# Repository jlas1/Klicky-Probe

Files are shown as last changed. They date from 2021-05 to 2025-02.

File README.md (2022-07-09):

# Klicky Probe
Microswitch probe with magnetic attachment, primarily aimed at CoreXY 3d printers.

Initially it was focused on the [Voron printers](https://vorondesign.com/) (V2.4, V1.8, Trident, V0) and derivatives, now it's been restructured to better allow other printers to be documented here.

The objectives for this project are:
- drop in replacement for Omron TL-Q5MC2 or PL-08N2 (you don't need to replace the toolhead), replacement of BLtouch probes
- soldering not required
- minimal adjustments required
- be able to detect all the print surfaces
- be as close to the hotend tip as possible
- highly repeatable and accurate probes
- less temperature variations
- no melting of its parts
- cheap to build
- reuse spare parts if possible

Most of the Klicky probe users are using klipper, there are some macros in here that ease the probing process, by automating the attach, dock and use of the probe.

Some work has been developed to have the same functionality on RRF.

It can also be used with the [automatic Z calibration](https://github.com/protoloft/klipper_z_calibration) klipper plugin to effectively calculate the Z offset from the probe and from the Z endstop if your printers supports a Z endstop triggered by the nozzle (like most Voron's do)

The inspiration for the Klicky Probe comes from the [Quickdraw](https://github.com/Annex-Engineering/Quickdraw_Probe) and the [Euclid probe](https://github.com/nionio6915/Euclid_Probe), it uses some concepts from each of the projects.

Updated instructions provided by StefanRaatz.
oc_geek and TurBoxxs were also a great help in refining and testing the CAD files.
Garrettwp provided the initial revised macro files.
User richardjm revised the macro variables and added some functions.
Mental created the initial macro and one of the first magnetically attached microswitch probes.

Without them, and some others this effort would not be in the current state, many thanks to them all.

It is working very well, if you decide to use it, give me feedback, either here, or on discord, my discord user is JosAr#0517.

If you want to donate something regarding this project, use this [link](https://paypal.me/Josar154) or [__Buy me some ABS!__](https://www.buymeacoffee.com/JosAr), thanks

# Upgrading from an earlier version

If you are upgrading from an earlier version, check the [klipper macros](./Klipper_macros) folder, it contains update instructions.

# Probe options

Right now, there are two probe attachment options, each with two probe types.

## Regular Klicky

First klicky probe, based on the [Quickdraw probe](https://github.com/Annex-Engineering/Quickdraw_Probe), with an added third magnet for added stability and fixed dock gantry setups.

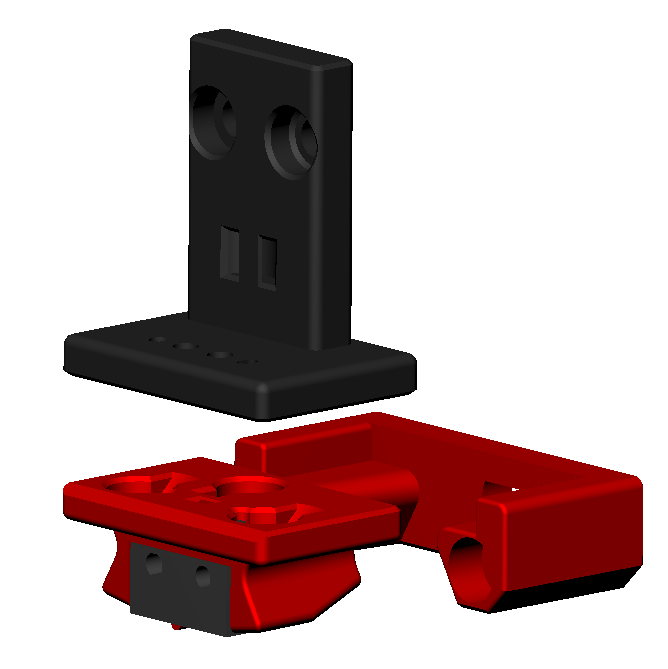
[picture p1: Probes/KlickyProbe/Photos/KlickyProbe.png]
klickyprobe


It uses magnets to secure the probe to the mount and also to make the electrical connection.
The magnets can be glued to prevent them from coming loose.
It supports a [microswitch probe](./Probes/KlickyProbe/) and [Unklicky](./Probes/Unklicky/) ([invented by DustinSpeed](https://github.com/majarspeed/Unklicky)) (self built probe, that so far surpasses the microswitches in common use) based probing.

### [Assembly instruction](./Probes/KlickyProbe/)

## KlickyNG

New enclosed magnets probe, it does not require glue to help prevent the magnets from coming loose, magnets are also self aligning.
This approach only uses common and easy to source parts.

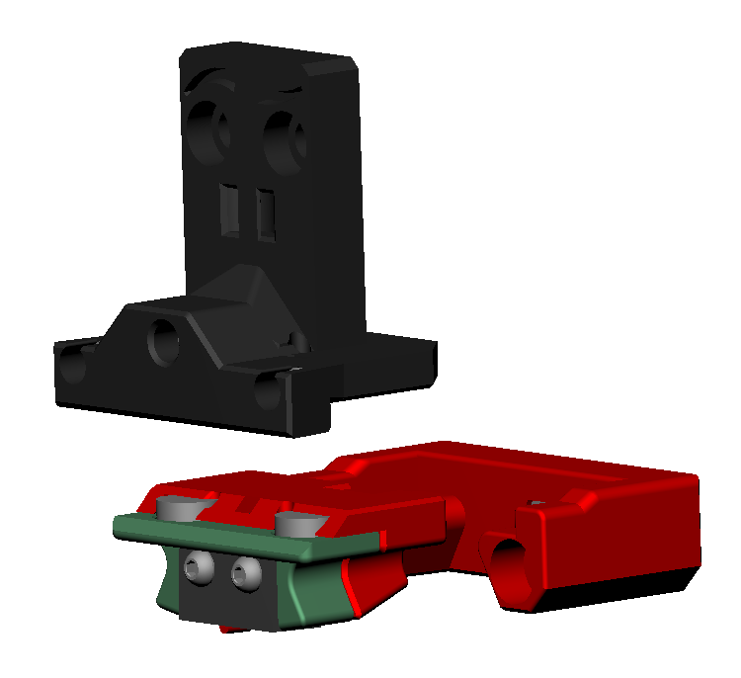
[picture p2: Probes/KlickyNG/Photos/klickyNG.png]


Also supports [microswitch probe](./Probes/KlickyNG/) and [Unklicky](./Probes/UnklickyNG/) ([invented by DustinSpeed](https://github.com/majarspeed/Unklicky)) (self built probe, that so far surpasses the microswitches in common use) based probing.

### [Assembly instruction](./Probes/KlickyNG/)

# Printers With detailed instructions and specific parts (by support order)

The specific parts with install, configuration, troubleshoot and recommended settings can be found on each printer page, linked below.

[Voron v2.4](./Printers/Voron/v1.8_v2.4_Legacy_Trident)

[Voron v1.8](./Printers/Voron/v1.8_v2.4_Legacy_Trident)

[Voron Legacy](./Printers/Voron/v1.8_v2.4_Legacy_Trident)

[Voron Trident](./Printers/Voron/v1.8_v2.4_Legacy_Trident)

[Voron v0](./Printers/Voron/v0)

[VCore 3.0/3.1 ](./Printers/Ratrig/VCore3.0_3.1)

[MercuryOne](./Printers/ZeroG/Mercury_One)

[Voron Switchwire](./Printers/Voron/Switchwire)

There are also [docks and mounts submitted by users](./Usermods) to support other printers and toolheads, you should check it out.

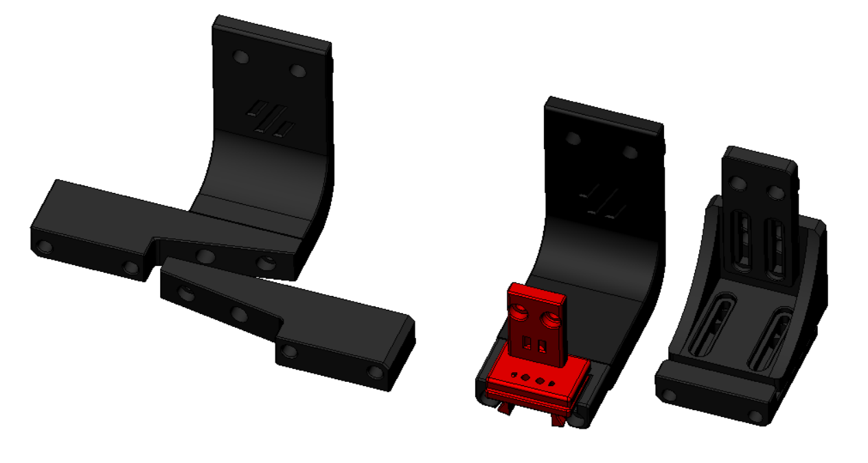
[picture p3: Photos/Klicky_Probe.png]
Klicky Probe image
klicky early version.

# Klicky components

All the compatible printers require:

* Toolhead mount (the thing that the probe attached to when it's being used)
* Klicky probe (there are three versions, all are interchangeable and compatible, more information on the specific printer page), what actually is used to probe the bed
* Probe dock (all the printers use the same)
* Probe dock mount (what attaches to the printer to dock the probe when not in use)

The CAD with all the files is located [Here](./CAD)

KlickyProbe STL's are now located on each probe type directory.

Printer specific STL are in each printer directory.

The klipper macros are [here](./Klipper_macros), the RRF [here](./RRF_macros).

## Probe accuracy

The probe accuracy output is better than a range of 0.025mm (difference between highest and lowest), and a standard deviation of 0.01mm.

## Print Settings

There are no need for supports, recommended settings are 4 perimeters/top/bottom, at least 23% infill, the STL's are already oriented, you only need to send them to the slicer.

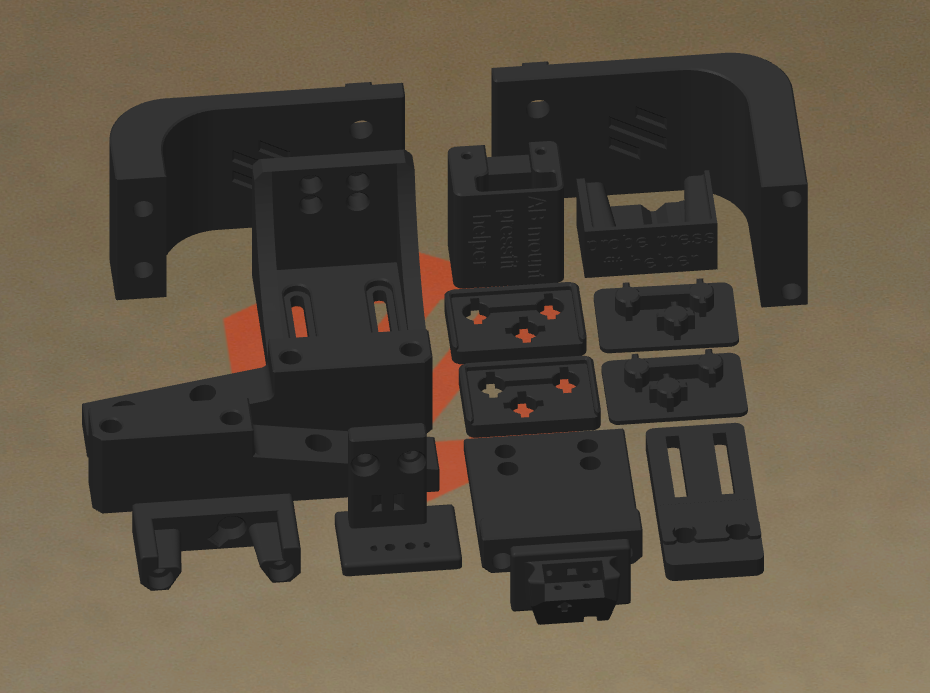
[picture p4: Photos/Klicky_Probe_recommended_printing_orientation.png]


Each printer family/version has it's own mounting options, Bill of Materials, assembly instructions and dock/attach setup.

# General Bill of Materials (BOM)

Tools:

- 1.5mm Drill (optional)
- Multimeter to check for Continuity 
- Super Glue
- Soldering Iron for the heat inserts

Probe BOM:

- 1x microswitch (the omron D2F-5 or D2F-5L (removing the lever) is recommended), D2F-1 and similar sizes microswitch also work
- 2x M2x10 mm self tapping
- some 6 mm x 3 mm magnets (it ranges from 8 to 10)
- some m5 screws
- some m3 screws
- some m3 heat inserts
- some m3 nuts

# Sourcing guide

To get the best experience, please consider purchasing from the trusted list of suppliers bellow.

[trusted suppliers list](./Sourcing.md)

# Assembled Klicky Probe on a Voron v2.4

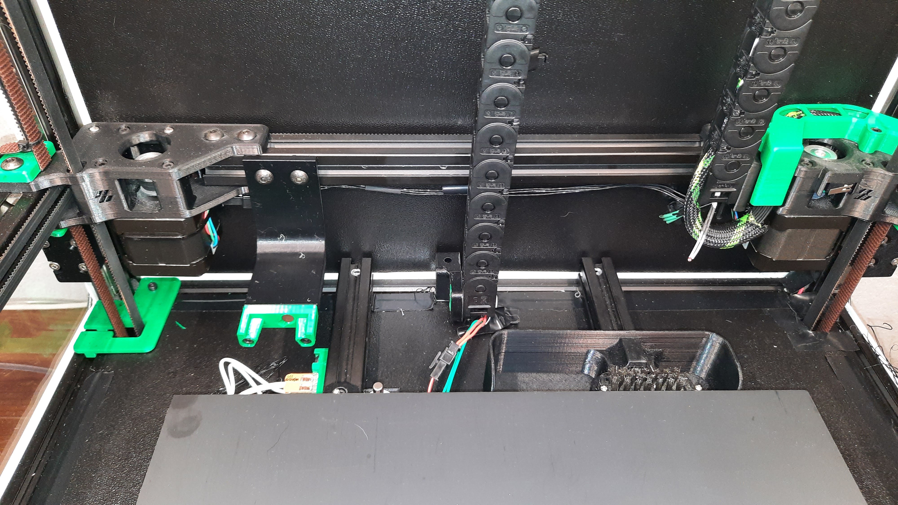
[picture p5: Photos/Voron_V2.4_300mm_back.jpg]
Assembled Klicky Probe
# 

# Dock and undock video

https://user-images.githubusercontent.com/16675722/122302371-eb9c4e00-cef9-11eb-91d3-3aded131bae0.mp4

It is working very well, if you decide to use it, give me feedback, either here, or on Voron discord, my discord user is JosAr#0517.

By standing on the shoulders of giants, lets see if we can see further.

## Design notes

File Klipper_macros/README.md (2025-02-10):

# Klipper macros

These macros are  based on the great Annex magprobe dockable probe macros "#Originally developed by Mental, modified for better use on K-series printers by RyanG and Trails", kudos to them.
That macro as since evolved into a klipper plugin that currently is pending inclusion in klipper, more information [here](https://github.com/Annex-Engineering/Quickdraw_Probe/tree/main/Klipper_Macros)

Would alse like to thank the Voron discord community and VoronDesign for all the work, suggestions and support that they have given to improve on the macros.

## Klipper change 20240313

Klipper `ACCEL_TO_DECEL` parameter of the `SET_VELOCITY_LIMIT` command has been deprecated, klicky macros used it on one location, that is now fixed on the versions going forward.

## New installation

The macros are currently separated by function, there is klicky-probe.cfg that should include the remaining files, this both keeps klipper's printer.cfg cleaner and allow for backward compatibility.

The remaining files are the klicky-macros.cfg that stores all the general macros (like the dock and attach macros, this file is required on all the printers), the klicky-variables.cfg where it's necessary to configure the dock location and do other printer specific configurations and the klipper helper files for specific functions.

The helper files work by expanding the standard klipper function with a attach and dock command, so that you can use all the klipper commands without the need to manually attach and dock the printer.

Right now the macros are divided in multiple files, that way it is much easier to upgrade, configure and maintain

| File | v2.4 | v1.8 | Legacy | Trident | Switchwire | v0 | Tiny-M | V-core3 | MercuryOne |
| --- | :---: | :---: | :---: | :---: | --- | :---: | :---: | :---: | --- |
| klicky-probe.cfg | :heavy_check_mark: | :heavy_check_mark: | :heavy_check_mark: | :heavy_check_mark: | :heavy_check_mark: | :heavy_check_mark: | :heavy_check_mark: | :heavy_check_mark: | :heavy_check_mark: |
| klick-variables.cfg | :heavy_check_mark: | :heavy_check_mark: | :heavy_check_mark: | :heavy_check_mark: | :heavy_check_mark: | :heavy_check_mark: | :heavy_check_mark: | :heavy_check_mark: | :heavy_check_mark: |
| klicky-bed-mesh-calibrate.cfg | :heavy_check_mark: | :heavy_check_mark: | :heavy_check_mark: | :heavy_check_mark: | :heavy_check_mark: | :heavy_check_mark: | :heavy_check_mark: | :heavy_check_mark: | :heavy_check_mark: |
| Klicky-quad-gantry-level.cfg | :heavy_check_mark: | :x: | :x: | :x: | :x: | :x: | :x: | :x: | :x: |
| Klicky-screws-tilt-calculate.cfg | :x: | :heavy_check_mark: | :heavy_check_mark: | :x: | :x: | :heavy_check_mark: | :heavy_check_mark: | :x: | :grey_question: |
| klicky-z-tilt-adjust.cfg | :x: | :heavy_check_mark: | :heavy_check_mark: | :heavy_check_mark: | :x: | :x: | :x: | :heavy_check_mark: | :heavy_check_mark: |

* klicky-probe.cfg (includes all the necessary files in klipper)
* klick-variables.cfg, stores all the Klicky variables, printer specific, should not be necessary to update very often
* klicky-bed-mesh-calibrate.cfg, bed mesh helper scripts, assumes bed mesh is already configured, includes a commented example, further help on setup [here](https://www.klipper3d.org/Bed_Mesh.html#bed-mesh)
* Klicky-quad-gantry-level.cfg, Quad Gantry Level helper script, allows on machines with four Z independent motors to level the bed automatically, assumes QGL is already configured (it's used on a V2.4 to level the gantry relative to the bed), further help [here](https://www.klipper3d.org/Config_Reference.html?h=quad#quad_gantry_level)
* Klicky-screws-tilt-calculate.cfg, screws tilt adjust helper script, knowing where the bed screws are, it will assist in leveling the bed by calculating on the number of times each screw should be rotated, assumes that the configuration is already defined, further help on setup [here](https://www.klipper3d.org/Manual_Level.html#adjusting-bed-leveling-screws-using-the-bed-probe)
* klicky-z-tilt-adjust.cfg, Z tilt adjust helper script, allows on machines with two or three Z independent motors to level the bed automatically, assumes that the configuration is already defined, further help on setup [here](https://www.klipper3d.org/Config_Reference.html?h=z_tilt#z_tilt)
* klicky-specific.cfg, place to put other configurations specific to your printer, like probe or bed mesh klipper configuration

Some printers, like the Voron v0 or Tiny-M don't have the probe as a standard configuration, so in those printers documentation there are extra klipper configurations that you need to use in order to configure the actual probe.

## printer.cfg configuration 

Download the appropriate files (or the zip containing them all and delete the ones that are not relevant) and upload it to your klipper Config folder.

```bash
cd ~/printer_data/config
wget https://raw.githubusercontent.com/jlas1/Klicky-Probe/main/Klipper_macros/Klipper_macros.zip
unzip Klipper_macros.zip
```

Check the klicky-probe.cfg, remove or comment the macros that are not required for your printer or that you do not want to implement.
Edit klicky-variables.cfg ([there are printers specific recommendations on the printer configuration page](https://github.com/jlas1/Klicky-Probe#printers-with-detailed-instructions-and-specific-parts-by-support-order)) for klicky to operate properly.

There are some configurations that need to be checked, otherwise your will run into **out of range** problems, that is by design.

Open your printer.cfg file, comment out *safe_z_home* or *homing_override*, if you have them (the macros will take care of homing) and add the following line before the "Macros" Section.

`[include klicky-probe.cfg]`

It should look like this:

```ini
#####################################################################
# 	Macros
#####################################################################
[include klicky-probe.cfg]
```

You now need to configure the probe pin, that is printer specific, and the details are on your printer configuration guide.

Regarding you print start and end macros, with the helper scripts implemented, they do not need to be changed.

If however you would like to reduce the times that the toolhead attaches and docks the probe, you can use Attach_Probe_Lock that prevents the probe to be docked after an operation that normally would dock the probe.

**BEWARE that the probe may hit the bed depending on what you are doing**.

When you don't need the probe attached anymore, run Dock_Probe_Unlock to dock and unlock the probe.

## Pre and Post macros for dock operations

If your setup requires a custom move, a macro to be called before attaching and docking, there are two macros **\_DeployDock** and **\_RetractDock** that are executed (if they are configured) when it's required for the dock to be ready for docking and attachment operations.

Currently, thanks to Kyleisah there is also support to use a simple servo setup, when a certain angle deploys the dock and another retracts it, you can find the following variables on klicky-variables.cfg.

```ini
#The following variables are used if the dock is deployed and retracted via a servo motor
variable_enable_dock_servo:  False    # Set to true if your klicky dock is servo-controlled
variable_servo_name:        'NAME'    # The name of the dock servo defined in printer.cfg under [servo]
variable_servo_deploy:          10    # This EXAMPLE is the value used to deploy the servo fully
variable_servo_retract:         11    # This EXAMPLE is the value used to retract the servo fully (initial_angle in [servo] config)
variable_servo_delay:         1000    # This is a delay to wait the servo to reach the requested position, be carefull with high values
```

On printer.cfg to add servo support, you need to add the following:

```ini
[servo klicky_servo]
pin: PC12
#   PWM output pin controlling the servo. This parameter must be
#   provided.
maximum_servo_angle: 180
#   The maximum angle (in degrees) that this servo can be set to. The
#   default is 180 degrees.
minimum_pulse_width: 0.00025
#   The minimum pulse width time (in seconds). This should correspond
#   with an angle of 0 degrees. The default is 0.001 seconds.
maximum_pulse_width: 0.0024
#   The maximum pulse width time (in seconds). This should correspond
#   with an angle of maximum_servo_angle. The default is 0.002
#   seconds.
```

To increase the servo strength, you should connect the servo 5v to a PSU instead of to the MCU.

## Status leds

Thanks to foonietunes we now have status leds support (specially useful for SB leds).

[You can read how to implement it here](https://github.com/VoronDesign/Voron-Afterburner/tree/sb-beta/Klipper_Macros).

## XY Sensorless homing 

If you are using sensorless homing, and have your own X and/or Y homing macros, you can use override the klicky macros behavior with your very own _HOME_X and _HOME_Y macros.

If they exist on your klipper configuration, klicky macro will use them instead of the default G28 commands.

## Euclid support

To support euclid side dock and undock, try these values

```python
#Attach move. final toolhead movement to attach the probe on the mount
#it's a relative move
Variable_attachmove_x:          -70
Variable_attachmove_y:            0
Variable_attachmove_z:            0

#Attach move2
Variable_attachmove2_x:          0
Variable_attachmove2_y:         40
Variable_attachmove2_z:          0

#Dock move, final toolhead movement to release the probe on the dock
#it's a relative move
Variable_dockmove_x:              0
Variable_dockmove_y:            -40
Variable_dockmove_z:              0
```

**you need to check what is the Z height of the Euclid Dock to possibly update the z moves above**

## Advanced users

**Beware going forward, you will leave the safety that the macros provide**

I recognize that some users are very technical and may want to write custom macros, so here are the only commands that you need to  attach and dock the probe, without any fail safes or checks.

### Probe attach commands

```python
# Probe entry location
G0 X{docklocation_x|int - attachmove_x|int - attachmove2_x|int} Y{docklocation_y|int - attachmove_y|int - attachmove2_y} F{travel_feedrate}
# Attach probe
G0 X{docklocation_x|int - attachmove2_x|int} Y{docklocation_y|int - attachmove2_y} F{travel_feedrate}
G0 X{docklocation_x} Y{docklocation_y} F{dock_feedrate}
# Probe exit location
G0 X{docklocation_x|int - attachmove_x|int} Y{docklocation_y|int - attachmove_y|int} F{release_feedrate}
```

### Probe dock commands

```python
# Probe entry location
G0 X{docklocation_x|int - attachmove_x|int} Y{docklocation_y|int - attachmove_y|int} F{travel_feedrate}
# Drop Probe to Probe location
G0 X{docklocation_x} Y{docklocation_y} F{dock_feedrate}
# Probe decoupling
G0 X{docklocation_x|int + dockmove_x|int} Y{docklocation_y|int + dockmove_y|int} F{release_feedrate}
G0 X{docklocation_x|int + dockmove_x|int - attachmove_x|int} Y{docklocation_y|int + dockmove_y|int - attachmove_y|int} F{release_feedrate}
```

The typical variables values are:

```ini
variable_travel_speed:          100    # how fast all other travel moves will be performed when running these macros
variable_dock_speed:             50    # how fast should the toolhead move when docking the probe for the final movement
variable_release_speed:          75    # how fast should the toolhead move to release the hold of the magnets after docking
#Dock move (if the dock is mounted on the back extrusion, these values can be left untouched)
Variable_dockmove_x:              0    # Final toolhead movement to release
Variable_dockmove_y:             40    # the probe on the dock
Variable_dockmove_z:              0    # (can be negative)
#Attach move (if the dock is mounted on the back extrusion, these values can be left untouched)
Variable_attachmove_x:           30    # Final toolhead movement to Dock
Variable_attachmove_y:            0    # the probe on the dock
Variable_attachmove_z:            0    # (can be negative)

Variable_attachmove2_x:           0    # intermediate toolhead movement to attach
Variable_attachmove2_y:           0    # the probe on the dock (can be negative)
Variable_attachmove2_z:           0    # (to be used as a last move before attaching the probe, suitable for Euclid)
```

**Again, be advised that these will not raize the bed to avoid hitting it, won't check if the probe is docked or attached. USE EXTREME CAUTION**

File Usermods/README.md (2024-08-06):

# Klicky usermods

Here you can find Klicky user submitted mods to support extra printers and toolheads, mods that support a printer with specific documentation (Like the Vorons ot the Vcore3) have a dedicated usermod directory in the specific printer directory.

All the compatible printers require:

* Toolhead mount (the thing that the probe attached to when it's being used), it's toolhead specific
* Klicky probe (there are three versions, all are interchangeable and compatible, more information on the specific printer page), what actually is used to probe the bed, the parts are equal on all the printers
* Probe dock (all the printers use the same), the parts are equal on all the printers
* Probe dock mount (what attaches to the printer to dock the probe when not in use), should be printer specific and not toolhead specific

The recommended macros can be found [here for klipper](..//Klipper_macros) macros and [here for RRF](../RRF_macros).

There are three types of user mod:

* Printer dock mount (identified by "dock mount")
* Toolhead probe mount (identified by "probe mount")
* Klicky Probe (identified by "probe")

| Owner | Descrption | Mod Type | Printer/Toolhead |
| --- | --- | --- | --- |
| TheMacBoy | [support arm for Ender 5 Plus with rails](./TheMacBoy) | dock mount  | Ender 5 Plus |
| TheMacBoy | [Klicky Probe mount for EVA](./TheMacBoy) | probe mount | EVA 2.2+ |
| DoubleT | [Klicky Probe mount for EVA Trihorn UHF fan duct](./DoubleT) | probe mount | EVA 2.4+ |
| SSerpente | [Klicky Probe mount for VzBot](./SSerpente) | dock mount  | VzBot |
| WhistlinRic | [UnklickyNG BFG in halves with m2x10](./WhistlinRic) | probe | N/A |
| SemperDiscere | [Klicky Probe for Dragon UHF Hotend](./SemperDiscere) | probe | Voron Dragon UHF |
| JarTheHead | [Klicky Probe for RtV6 Revo Nozzle Adapter](./JarTheHead) | probe | Voron Revo |

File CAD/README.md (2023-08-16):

CAD files

KlickyProbe_v2_v44
Initial release of the V2 klicky, with a 2mm shorter probe dock. Probe dock mounts adjusted accordingly

KlickyProbe_v2_v50
corrected dock mount fixed distance, it was 2 mm short

KlickyProbe_v2_v51
added MercuryOne probe dock

KlickyProbe_v2_v53
added VCore3 probe dock and EVA mount

KlickyProbe_v2_v54
added V0.1 Mosquito Cowling

KlickyProbe_v2_v55
corrected V0.1 integrated Mosquito Cowlings

KlickyProbe_v2_v56
updated the probe dock to have back inserted magnets, it's not possible now for the dock magnet to touch the probe one

KlickyProbe_v2_v57
Added V0.1 integrated Voron Revo Cowling

KlickyProbe_v2_v57
Added initial Switchwire servo dock

KlickyProbe_v2_v58
Changed the servo arms magnets, can't come loose now during a print

KlickyProbe_v2_v60
added UHF probe
beefed up the probe AB/SB mount and adopted probe mount holder from EAMARS

KlickyProbe_v2_v61
added V0.2 cowling with new magnet sizes option

KlickyProbe_v2_v62
added V0.2r1 cowling

KlickyNGProbe_v4
Reduced the probe socket height, to better handle 2.7mm magnets

KlickyNGProbe_v5
Added a 3mm socket height, to better handle 3mm magnets

KlickyNGProbe_v6
Improved AB/SB mount and front attachment, revised back probe magnet seat

KlickyNGProbe_v7
reduced AB/SB mount front hole size, added better magnet installation helper, extended the dock magnet wall from 0.44mm to 1mm

KlickyNGProbe_v8
improved probe body, reducing probe tilt

KlickyNGProbe_v9
probe body tilt further reduced, lower and smaller dock mount (no need to change Y offset)

KlickyNGProbe_v10
improved Unklicky cap function, now the cap has 2.7 and 3mm versions, most probes have only one body
added V0.1 compatibility
added Tiny-M compatibility
added V0 and UHF probes

KlickyNGProbe_v11
improved Unklicky cap function
added V0.2 cowling with new magnet sizes option

KlickyNGProbe_v12
added V0.2r1 cowling

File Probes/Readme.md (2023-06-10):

# Probe options

Right now, there are two probe attachment options, each with two probe types.

## Regular Klicky

First klicky probe, based on the [Quickdraw probe](https://github.com/Annex-Engineering/Quickdraw_Probe), with an added third magnet for added stability and fixed dock gantry setups.

klickyprobe

It uses magnets to secure the probe to the mount and also to make the electrical connection.
The magnets can be glued to prevent them from coming loose.
It supports a [microswitch probe](./KlickyProbe/) and [Unklicky](./KlickyProbe/) ([invented by DustinSpeed](https://github.com/majarspeed/Unklicky)) (self built probe, that so far surpasses the microswitches in common use) based probing.

#### [Assembly instruction](./KlickyProbe/)

## KlickyNG

New enclosed magnets probe, it does not require glue to help prevent the magnets from coming loose, magnets are also self aligning.
This approach only uses common and easy to source parts.

klickyNGprobe

Also supports [microswitch probe](./KlickyNG/) and [Unklicky](./UnklickyNG/) ([invented by DustinSpeed](https://github.com/majarspeed/Unklicky)) (self built probe, that so far surpasses the microswitches in common use) based probing.

#### [Assembly instruction](./KlickyNG/)

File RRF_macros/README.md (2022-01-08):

I have zero experience with RRF, but Noodle obviously knows and has done the necessary work to get both klicky and [autoZ](https://github.com/protoloft/klipper_z_calibration) working.

You can look up the firmware configuration on a Voron v2.4 for the [Klicky RRF macros](https://github.com/pRINTERnOODLE/RRF-klicky-probe-voron-2.4.git) and for the [Klicky plus AutoZ](https://github.com/pRINTERnOODLE/Auto-Z-calibration-for-RRF-3.3-or-later-and-Klicky-Probe).

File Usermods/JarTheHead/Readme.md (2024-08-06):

## [JarTheHead's](https://github.com/JarTheHead) Klicky Probe for the RtV6 Revo nozzle adapter
This is a modification of Klicky probe for use with a Revo nozzle adapter. It is primarily remixed from [SemperDiscere's DragonUHF probe](https://github.com/JarTheHead/Klicky-Probe/tree/main/Usermods/SemperDiscere). The RtV6 adds about 6mm of height to a standard Revo nozzle when using a typical RepRap nozzle. Only designed with Klicky (no plans for NG or UnKlicky).

## Build
Build Is Similar to the AB Mount. 
- Solder wires to the outside pins of the D5F-L switch
- Remove Lever from switch
- Estimate wire length and cut
- Strip Wires
- Feed wires through Holes
- Seat Magnets
- Test continuity
- Trim wires
- Screw switch to Main Body

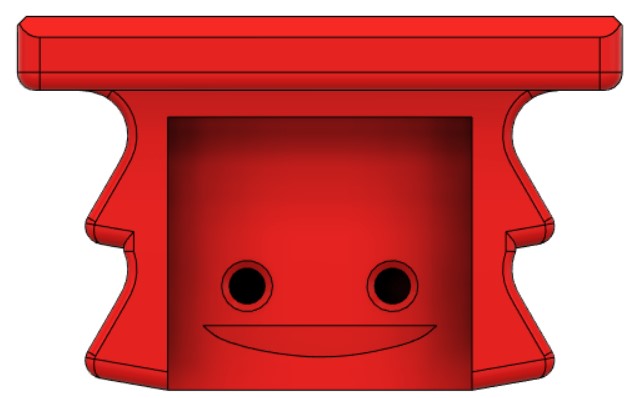
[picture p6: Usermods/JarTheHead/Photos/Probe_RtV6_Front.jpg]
Klicky probe Front


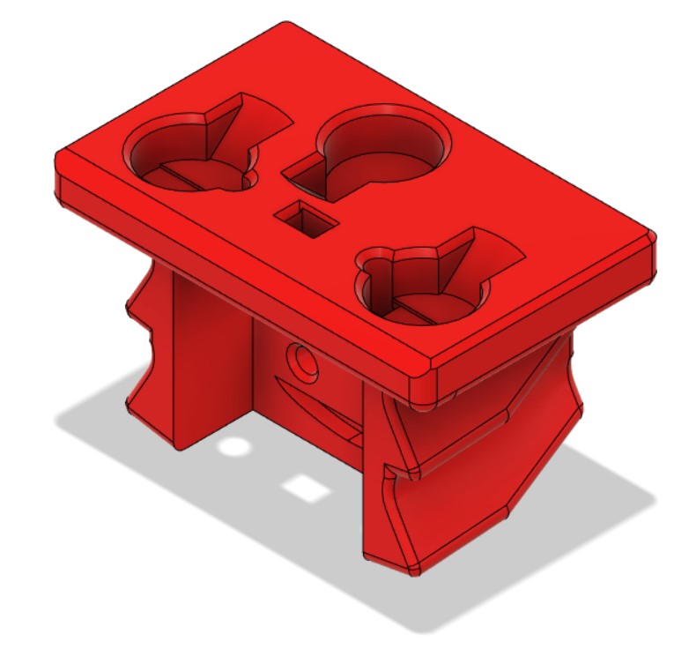
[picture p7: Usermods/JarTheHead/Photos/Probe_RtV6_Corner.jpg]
Klicky probe 3/4


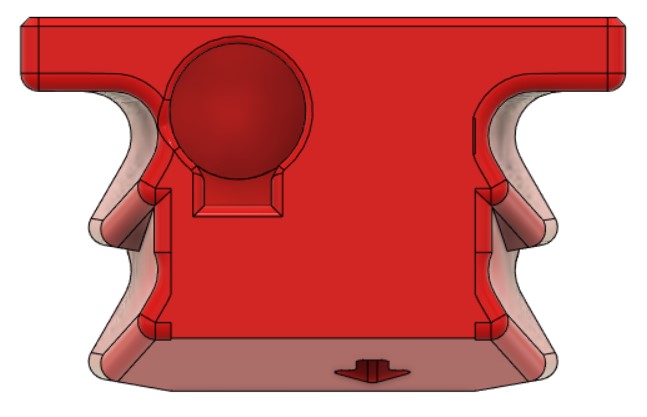
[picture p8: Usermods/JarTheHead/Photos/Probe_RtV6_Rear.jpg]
Klicky probe Rear

## Source Klicky probe file
[Klicky Probe](../../CAD/KlickyProbe_v2_v59.step)

## BOM:
| Qty | Name |
| --- | --- |
| 4 | 6x3 Magnets |
| 2 | M2 10mm |
| 2 | 24 ga wire |
| 1 | Omron D2F-5 switch (or similar) |

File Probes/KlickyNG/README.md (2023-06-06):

# Klicky Probe NG (Next Generation) (or No Glue :-) )
Microswitch probe with magnetic attachment, primarily aimed at CoreXY 3d printers, with enclosed magnets, don't fall, don't need to be glued.

This version has been used on tens (hundreds ?) of machines, so it can be considered functional and safe.
For new setups and due to it's easier assembly i would recommend the KlickyNG over Klicky regular for new builds.

The objectives for this project are:
- drop in replacement for Omron TL-Q5MC2 or PL-08N2 (you don't need to replace the toolhead), replacement of BLtouch probes
- no soldering required
- minimal adjustments required
- be able to detect all the print surfaces
- be as close to the hotend tip as possible
- highly repeatable and accurate probes
- less temperature variations
- no melting of its parts
- reuse spare parts if possible
- no need to use hard to source parts
- no need to glue the magnets

For now this document will only deal with KlickyNG-specific wiring; for all the rest of the configuration, please follow the [main guide](https://github.com/jlas1/Klicky-Probe).

The inspiration for the Klicky Probe comes from the [Quickdraw](https://github.com/Annex-Engineering/Quickdraw_Probe) and the [Euclid probe](https://github.com/nionio6915/Euclid_Probe), it uses some concepts from each of the projects, but with this version, it expands on the concept, as the method that it uses was developed independently. 

Please check the main Klicky repository for all the people that helped this project, for NG, would like to thank (in no specific order) Dustinspeed, Drachenkatze, clee, maz and whoppingpochard.

If you want to donate something regarding this project, use this [link](https://paypal.me/Josar154) or [__Buy me some ABS!__](https://www.buymeacoffee.com/JosAr), thanks

Without further delay, here is the new version with enclosed magnets:
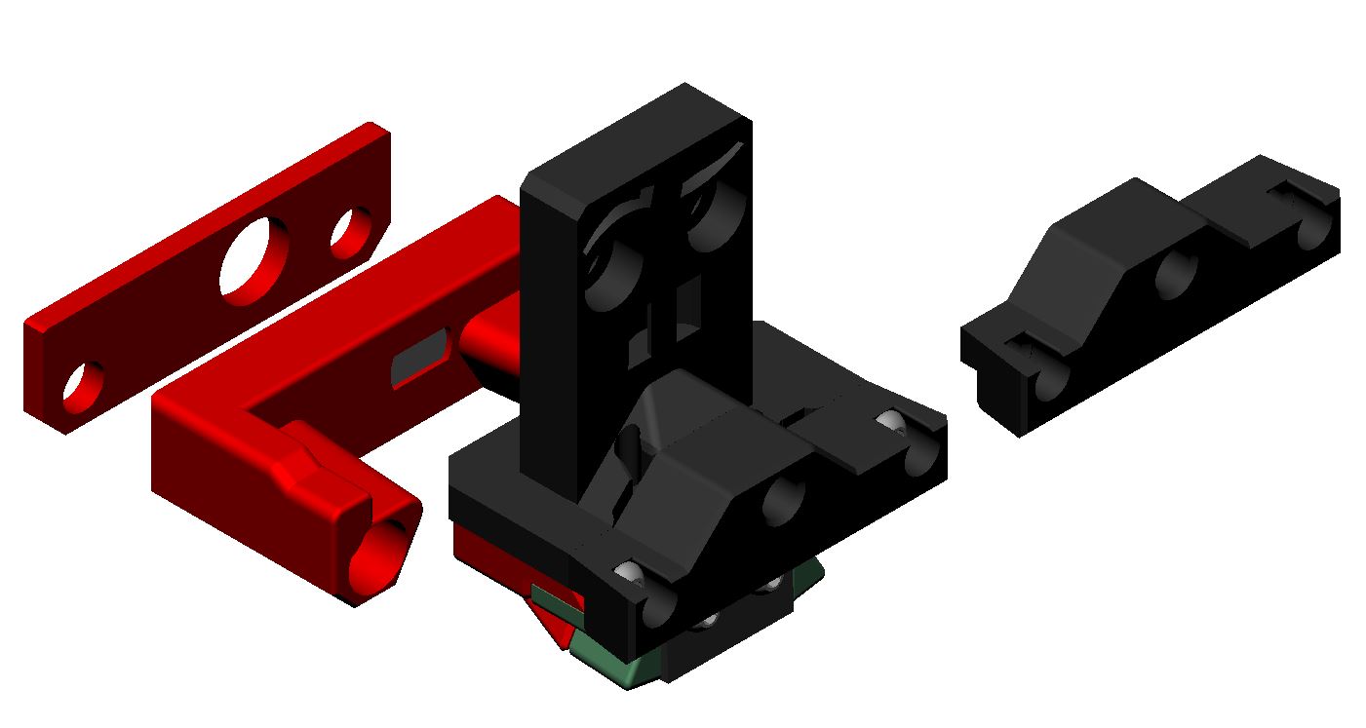
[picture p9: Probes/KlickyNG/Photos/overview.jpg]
Klicky Probe image


The eyebrows are clee+whoppingpochard's design.

# KlickyNG support

For now, only printers compatible with Voron StealthBurner/AfterBurner are compatible, as the NG mount has changed significantly and needs to be ported to the other mounts.

- [The CAD with all the files](../../CAD)
- [STL Files](./STL)

The arms are compatible with both Klicky and KlickyNG.

There is also [an exploded view](https://youtu.be/mlyU2tHjebo).

## Print Settings

There is no need for supports; recommended settings are 4 perimeters/top/bottom, at least 23% infill. The STL's are already oriented for you, so you only need to send them to the slicer.

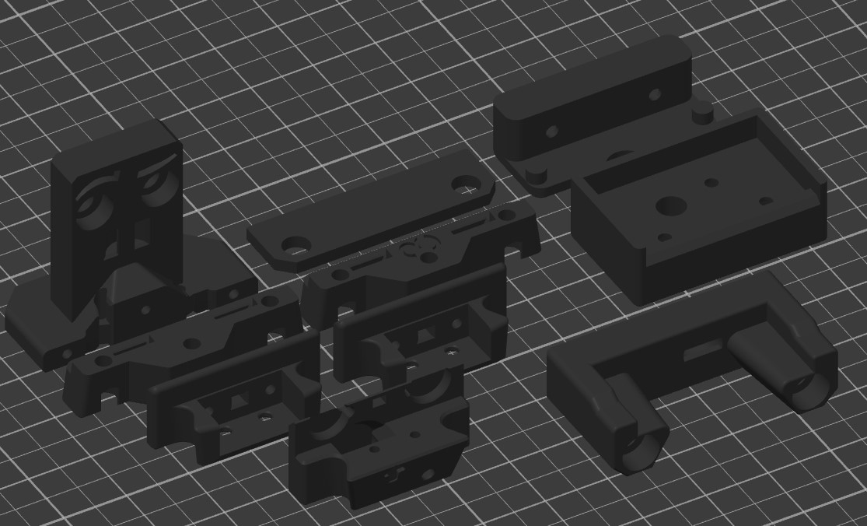
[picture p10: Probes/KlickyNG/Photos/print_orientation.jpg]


## Required parts

| | |
| :---: | --- |
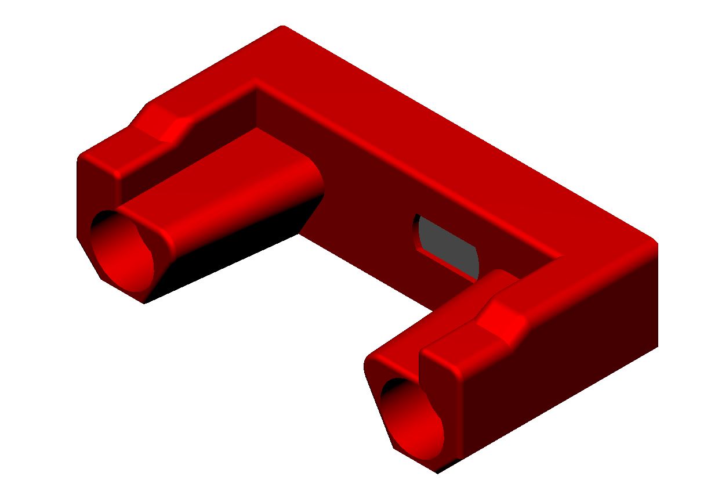
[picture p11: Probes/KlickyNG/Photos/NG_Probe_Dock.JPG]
NG_Probe_Dock
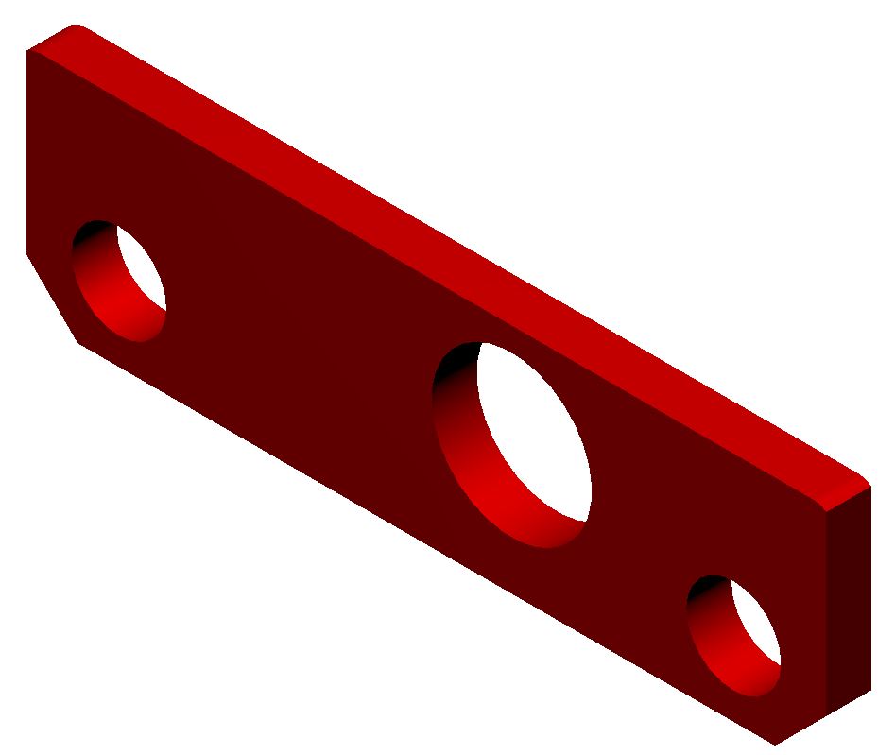
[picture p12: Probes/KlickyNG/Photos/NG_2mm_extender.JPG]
NG_2mm_extender
|  | If you want to reuse your old Klicky dock, it needs to use this setup for the back magnet. It will also be necessary to print the 2mm NG extender, as the dock needs to be 2mm longer. |
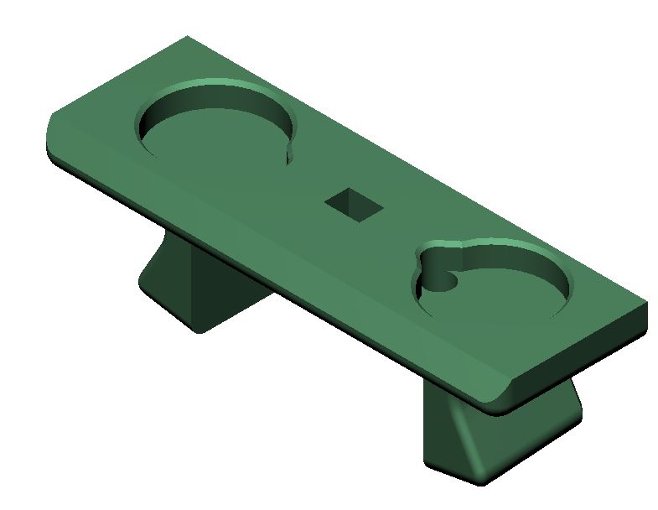
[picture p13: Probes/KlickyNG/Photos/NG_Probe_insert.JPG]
NG_Probe_insert
|  | Probe Insert, required to hold the switch and the two magnets that make the electrical connection, two versions; one for around 2.75mm (instead of 3mm) height, and one for actual 3mm-height magnets |
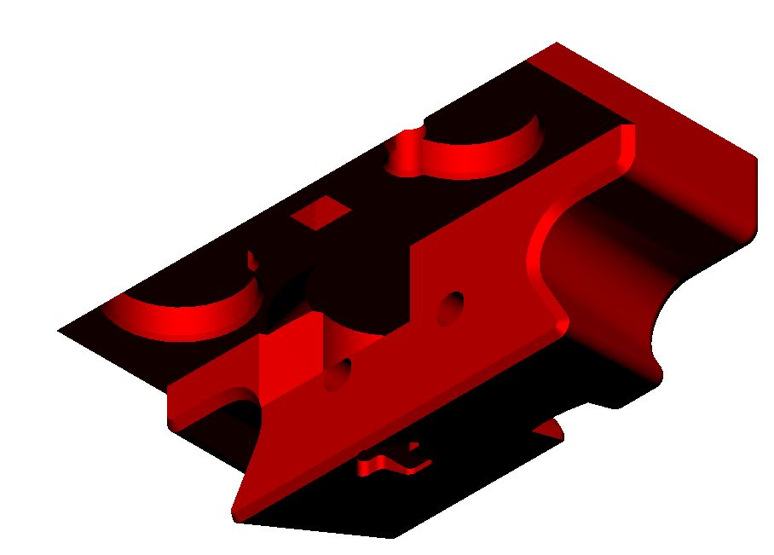
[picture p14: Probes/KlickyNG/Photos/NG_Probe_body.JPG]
NG_Probe_body
|  | Probe body, required to prevent the two front magnets from escaping the probe, holds the third magnet to help attach the probe to the mount and the back magnet to secure it to the dock. |
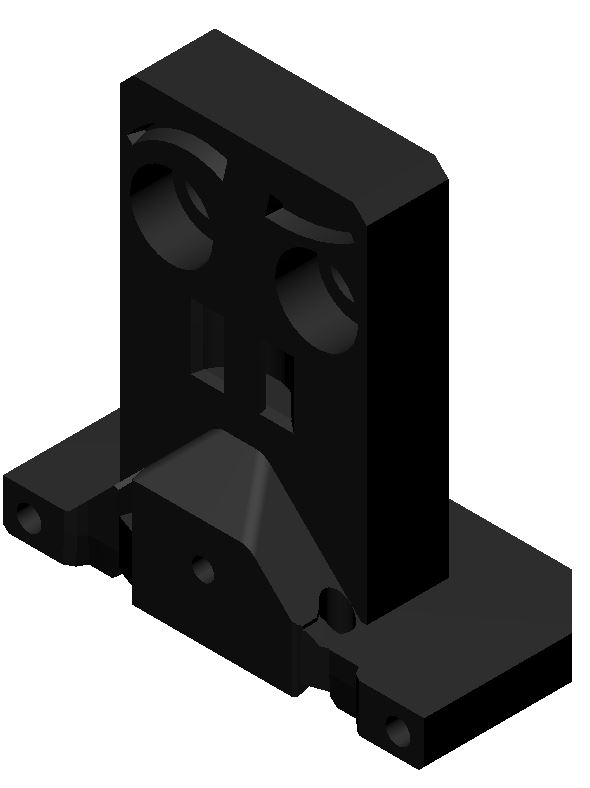
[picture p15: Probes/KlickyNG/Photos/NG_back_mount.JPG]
NG_back_mount
|  | Mount back, mounts to the AB/SB, holds the third magnet and the wire connections |
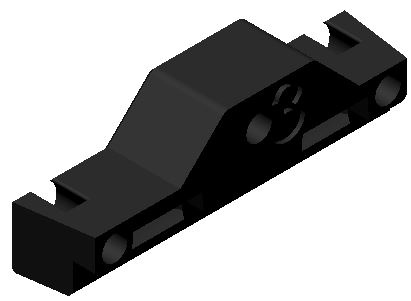
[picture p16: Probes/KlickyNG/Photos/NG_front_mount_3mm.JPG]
NG_front_mount_3mm
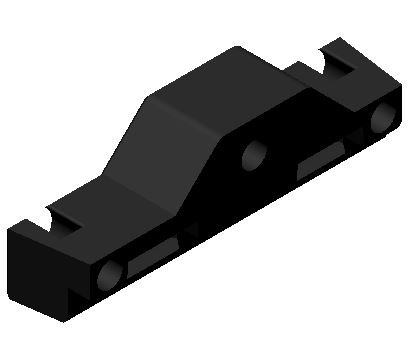
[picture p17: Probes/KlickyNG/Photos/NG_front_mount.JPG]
NG_front_mount
|  | Mount front, two versions; one for around 2.75mm (instead of 3mm) height, and one for actual 3mm-height magnets |

## Optional parts

| | |
| :---: | --- |
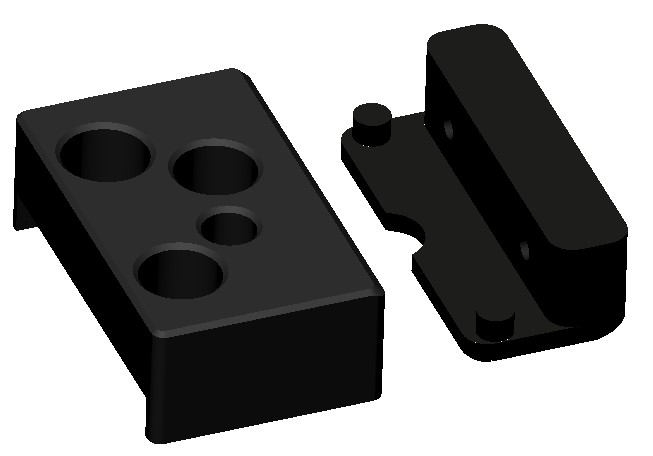
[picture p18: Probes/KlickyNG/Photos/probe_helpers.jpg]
NG_Probe_Dock
|  | To help with magnet installation (they can be very powerful and interact with each other before final assembly), you can use these parts, they require 3 more magnets (can be reused). |

# Bill of Materials (BOM)

- 1x microswitch (the Omron D2F-5, or D2F-5L with the lever removed, are recommended, but similar-sized microswitches like D2F-1 and KW10 will also work)
- 30cm of wire, AWG22 or similar
- 5 M2x10mm self-tapping screws
- 8x 6mm diameter x 3mm height magnets (add 3 more if you want to do the magnet helpers)
- 2x M3x18mm/M3x20mm screws

# Build Process

First, assemble the required materials.

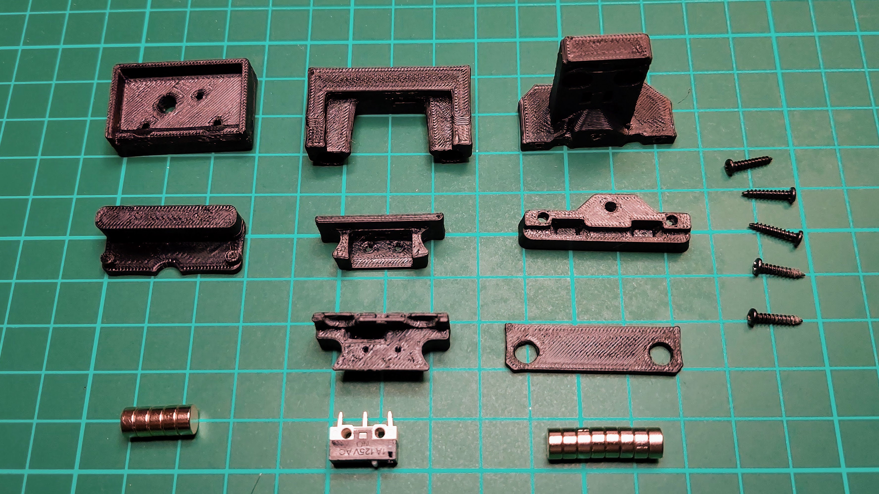
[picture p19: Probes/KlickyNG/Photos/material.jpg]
material


## Probe assembly

- Put one magnet on the back groove of KlickyNG_Probe_body, and add another to the matching hole on the KlickyNG_cap_magnet helper.
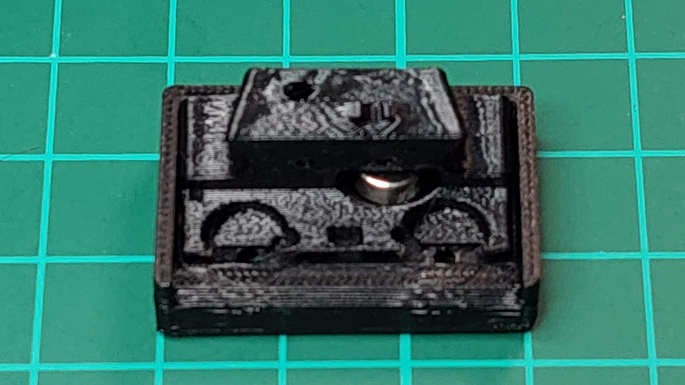
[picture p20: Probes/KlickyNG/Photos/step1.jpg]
step1
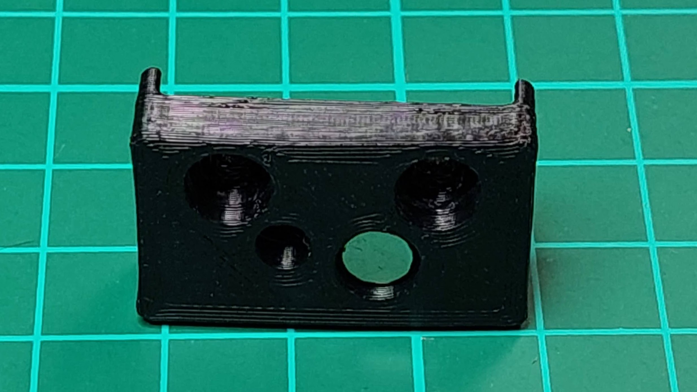
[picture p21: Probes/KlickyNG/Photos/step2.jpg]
step2
   
  
- Next, insert two magnets on the front sockets KlickyNG_Probe_body Body. These magnets should have the inverted polarity of the back magnet. After inserting each one, make sure to add the corresponding magnet to the magnet helper, it will help keep the magnets in place during assembly.
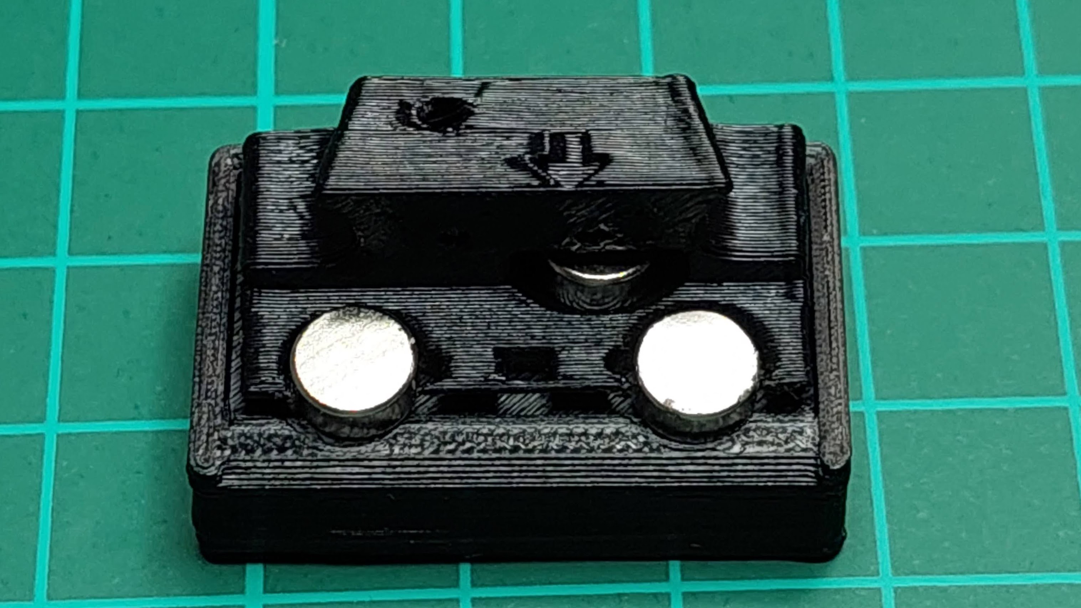
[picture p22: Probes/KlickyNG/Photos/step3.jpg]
step3
  

- Now, place the insert on the body (select either the regular insert or the 3mm one), aligning the magnets and making sure that the front magnets do not move out of place, attach the switch (note the arrow pointing to the switch pin) secure with the M2x10 screws.
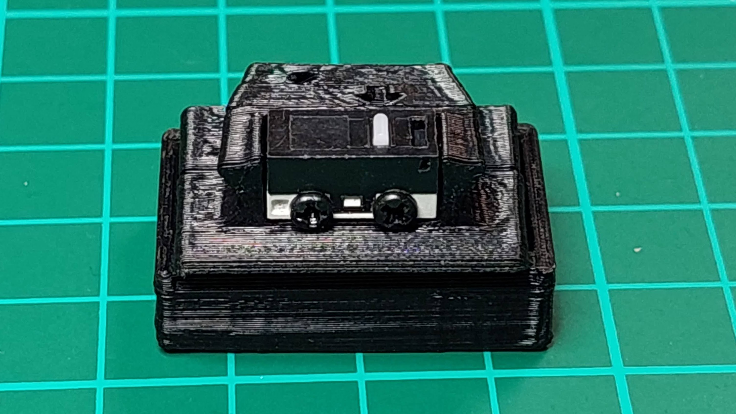
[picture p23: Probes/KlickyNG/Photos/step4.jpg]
step4
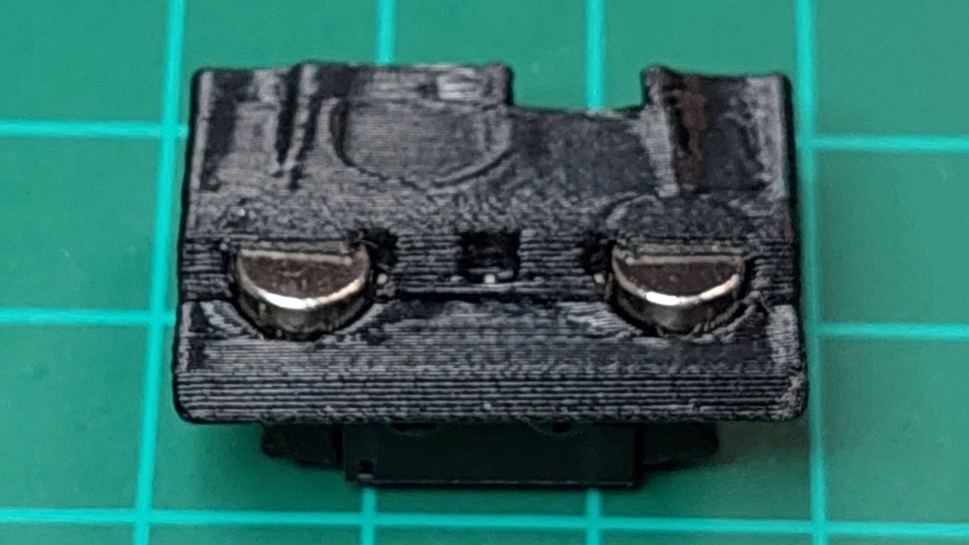
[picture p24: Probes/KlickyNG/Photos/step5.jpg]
step5
   

- (left to right) insert a magnet on the dock, via the back hole. Then place a magnet on the front of the dock and insert it on the back pocket of the probe, taking care to follow the same magnetic orientation, finally make sure the probe docks properly.
  
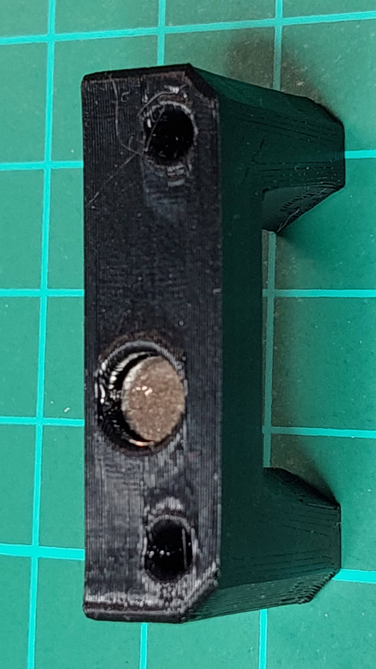
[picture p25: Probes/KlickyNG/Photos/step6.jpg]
step6
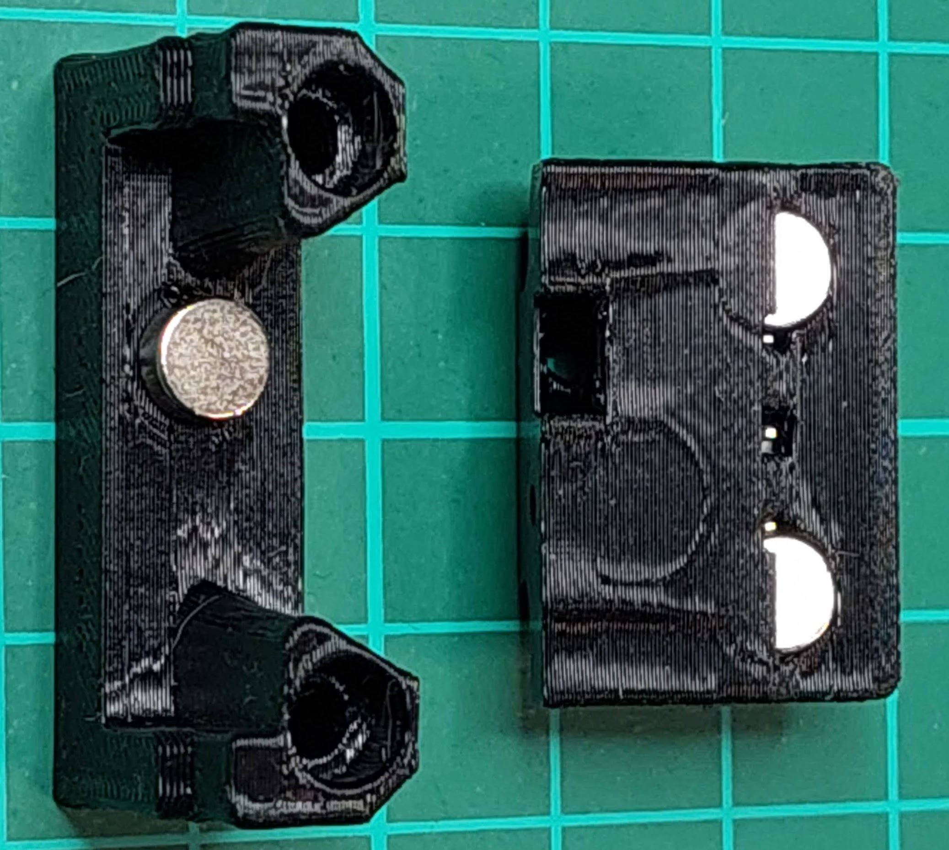
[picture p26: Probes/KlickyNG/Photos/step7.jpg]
step7
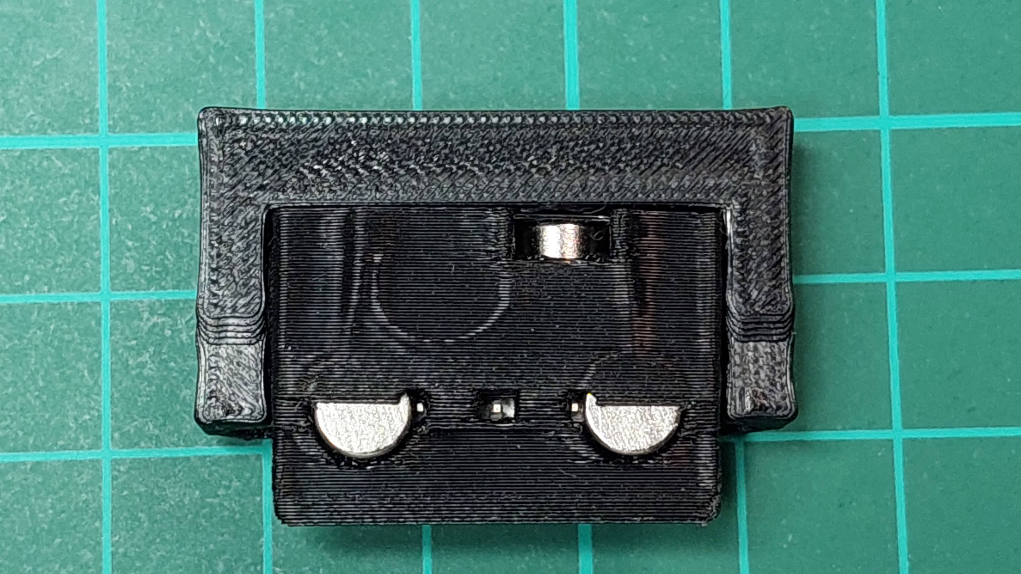
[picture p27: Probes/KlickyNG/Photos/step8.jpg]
step8
    

## AB/SB mount assembly

- Cut the 30cm of wire in half to create two 15cm lengths of wire. Remove 7-8mm of insulation, and rotate the core to prevent loose wires.
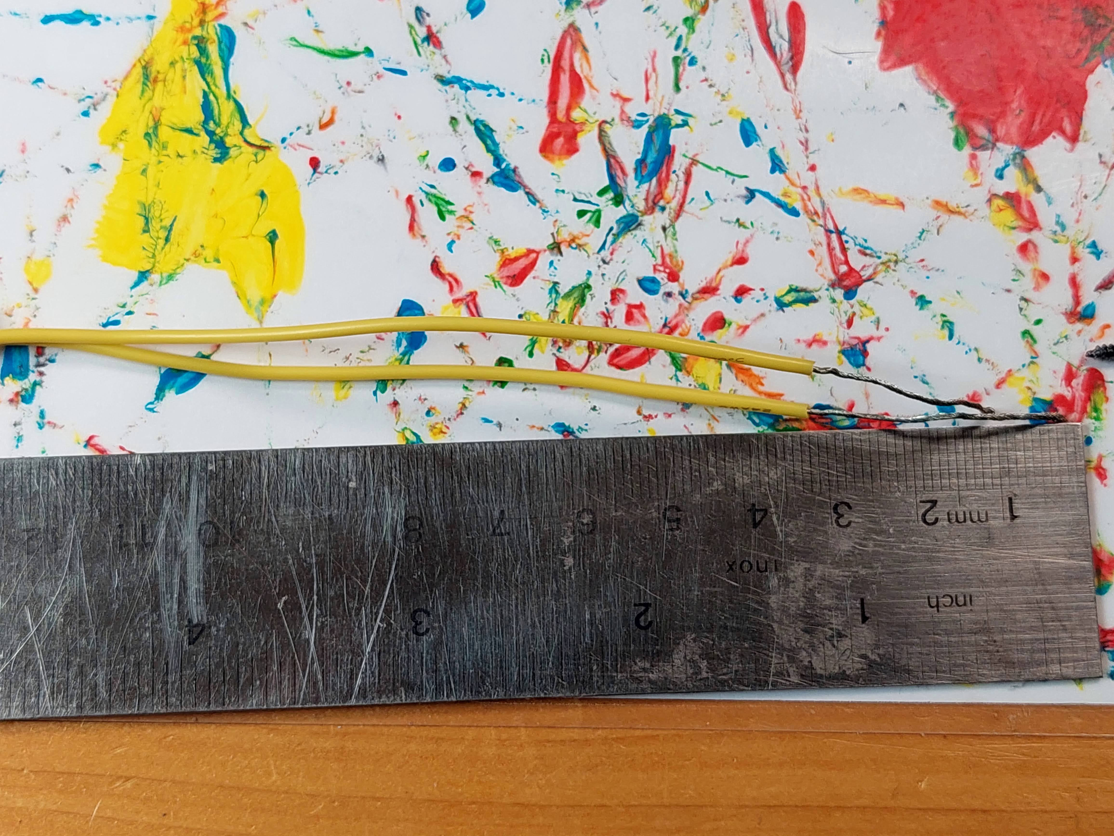
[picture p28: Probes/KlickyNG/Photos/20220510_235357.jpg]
  
- Insert the wire on the holes on the back mount
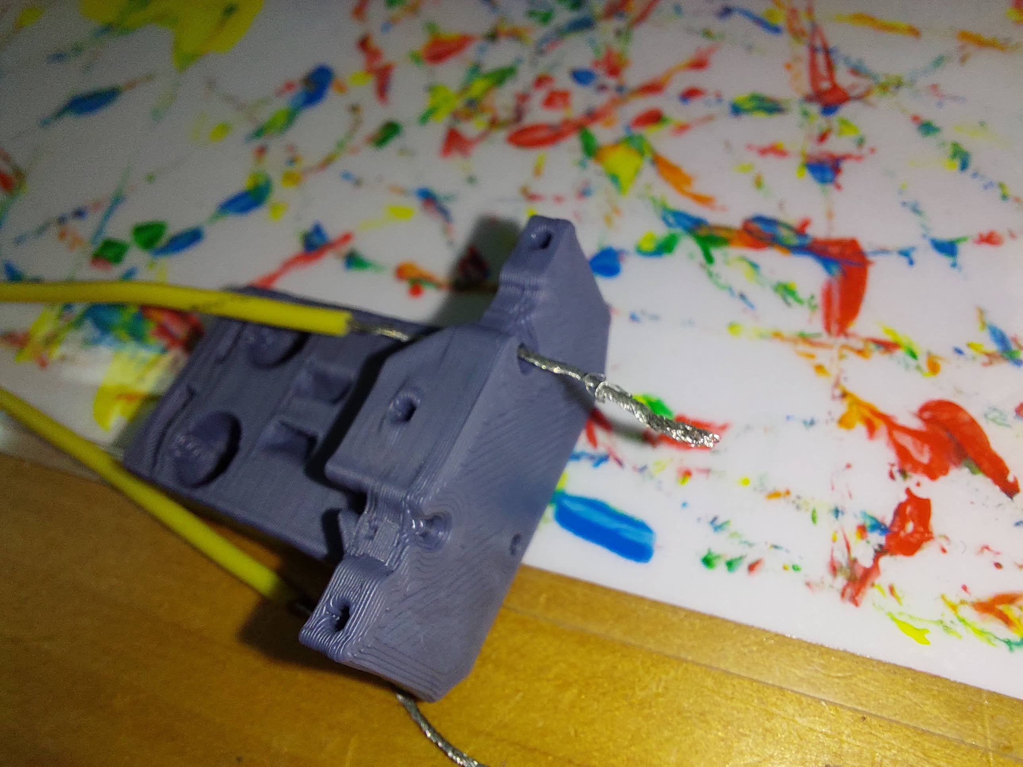
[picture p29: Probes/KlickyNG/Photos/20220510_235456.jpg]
  
- Rotate the wires around the other end to prevent them from escaping when the mount is being assembled
  
- Put two magnets on top on the probe front magnets
  
- Insert the correct front mount on the magnets so that they remain attracted to the probe.
  
- with the magnets and front secure, joint the mount front and back with an m2 screw
  
- Now, complete with the remaining two m2 screws that will keep the front level
  
- Attach another magnet on the 3rd probe magnet
  
- Respecting its polarity, put it into the mount back magnet socket
  
- The mount is now assembled!
  |  |  |
  | ------------------------------------------------------------ | ------------------------------------------------------------ |

## Check Your Work

Before anything, make sure the magnet orientations are correct. Go
through the assembly instructions again to ensure correct orientation.
Below are a bunch of checks assuming correct magnet orientation.

- Ensure that the AB/SB mount wires and the magnets are making contact

  Probe Magnets and Wire Making Contact

- If you have a multimeter handy, use it to check for continuity. Touch
  the bare wire on the top of the mount with one probe and the magnet
  on the opposing side with the other probe and check for continuity.

  Mount Continuity Check using Multimeter

- Ensure that the probe magnets and the microswitch leads are touching

  Probe and switch Making Contact

- Once again, if you have a multimeter handy, check for continuity by
  touching the two magnets with your multimeter probes.

  Probe magnets and switch continuity check

- When you are first installing the AB/SB mount, don't tightening the bolts
  down all the way. Make sure the mount can still move since we need to adjust how far the mount sits above the probe/dock.

  Loose AB mount bolts to allow for height adjustments

- Move the toolhead by hand to allow for the mount to sit right above
  the probe. There should be a hairs worth of gap between the mount and
  the probe. Once the correct height has been established, lock in the
  position by tightening down the bolts.

  Loose AB mount bolts to allow for height adjustments

- You should now be able to move the toolhead back by hand and ensure
  that the probe attaches correctly.

  Probe attaching to mount properly

## Final thoughts

For the installation, you should now replace the dock (or add the extender to your existing dock) and mount the probe mount to AB or SB and test it. You shouldn't need to change any configuration on your printer, if Klicky was already running without problems.

I have tested Aliexpress N35, N42 and N45 (graciously provided by Drachenkatze) with over 2000 attach/probe/dock without a single probe or dock operation failure.

Please test and report, but remember, it's still under development.

It is working very well for me. If you decide to use it, please send me feedback, either here, or on Voron discord. My discord username is `@JosAr#0517`.

By standing on the shoulders of giants, let's see if we can see further.

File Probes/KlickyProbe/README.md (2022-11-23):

# Klicky Probe
Microswitch probe with magnetic attachment, primarily aimed at CoreXY 3d printers.

KlickyProbe

The objectives for this project are:

- drop in replacement for Omron TL-Q5MC2 or PL-08N2 (you don't need to replace the toolhead), replacement of BLtouch probes
- no soldering required
- minimal adjustments required
- be able to detect all the print surfaces
- be as close to the hotend tip as possible
- highly repeatable and accurate probes
- less temperature variations
- no melting of its parts
- reuse spare parts if possible
- no need to use hard to source parts

## Print Settings

There is no need for supports; recommended settings are 4 perimeters/top/bottom, at least 23% infill. The STL's are already oriented for you, so you only need to send them to the slicer.

print_orientation

## Required parts

| NG_Probe_Dock | Klicky dock, it secures the probe to the dock via an extra magnet.<br />Allows to pull the probe by at least 2mm away |
| :---: | --- |
| Probebody | Probe body, there are 4 probe body's:<br />KlickyProbe v2, in the image, classical klicky probe<br />Long version, to be used on small printers, can reach under the nozzle to increase probe area<br />Longer version, to be used on small printers, can reach under the nozzle to increase even more probe area<br />XL version, classical probe extended by 12 mm useful for UHF hotends |

The required files are located here:

- [CAD files](../../CAD)
- [STL files](./STL)

# Bill of Materials (BOM)

- 1x microswitch (the Omron D2F-5, or D2F-5L with the lever removed, are recommended, but similar-sized microswitches like D2F-1 and KW10 will also work)
- 30cm of wire, AWG22 or similar
- 2 M2x10mm self-tapping screws
- 5x 6mm diameter x 3mm height magnets
- 2x M3x18mm/M3x20mm screws

# Build Process

## Probe assembly

For the probe assembly you need the following parts:

- [ ] 1x microswitch
- [ ] 2x M2x10 mm self tapping
- [ ] 4x 6 mm x 3 mm magnets
- [ ] 1.5mm Drill (optional)
- [ ] Multimeter to check for Continuity 
- [ ] Super Glue



Maybe you need to clear the holes for the microswitch, a 1.5mm drill bit should work fine.

Install the microswitch so that the arrow on the probe body is pointing to the little switch.





Then take your self tapping screws and screw the microswitch in place.



**Notice, there is an alternative method to install the magnets, that seems to improve fitting and results please read the instruction until the end and then decide on what is the bet method for you,**

Before placing the magnets, use some super glue on the holes (not a lot, just a drop), avoid the switch parts.

You want to install the magnets in the way that the ones which are connected to the microswitch, have the same polarity  The 3rd magnet should have the inverse polarity, you can use the included pressfit helpers to help in securing the probe when you are inserting the magnets.

There is no need for soldering, the probe microswitch connectors are press-fit on the magnets, they should remain with the top above the probe plastic.



Don't forget to install the magnet which holds the probe to the probe dock, make sure it is fully inserted.

As the last step of the probe assembly check if you have continuity between these two magnets



If you have a normally closed switch (as you should), then you should have a current flow, so continuity is established. When you press the switch you should lose continuity. When you have a normally open switch then the behavior is the other way around.

### Alternative installation method (by [kyleisah](https://github.com/kyleisah) and [DrachenKatze](https://github.com/DrachenKatze)  (who came up with the idea)

- Insert switch into probe and install screws
- Install stripped wire leads into probe mount
- Apply dabs of glue to probe, and quarter-install 2 magnets into each hole, making sure to invert the polarity for the rear probe magnet hole
- Apply dabs of glue to the probe mount and line up the magnets from  the probe to the magnet holes of the mount and press them in best you  can so they stay in the holes
- Using the press fit tools, force the probe and mount together so they bottom out against each other.
- Do not pull the probe and mount apart, slide them apart and allow the glue to cure.
- After the glue has sufficiently cured (read the label) slide the  mount and probe back together so the magnets realign and check for  continuity at the ends of the probe leads.

## AB/SB Mount

If you are going to use a AB/SB mount, please proceed to it's [instruction here](./ABSB_mount.md), otherwise proceed with the setup instructions of your printer.

## Final thoughts

For the installation, you should now install the dock (according with your printer instructions) and mount the probe mount.

It is working very well for me. If you decide to use it, please send me feedback, either here, or on Voron discord. My discord username is `@JosAr#0517`.

By standing on the shoulders of giants, let's see if we can see further.

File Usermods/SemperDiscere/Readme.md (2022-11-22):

## SemperDiscere's Klicky Probe for the Phaetus DragonUHF with Standard Dragon Mount

> Created by: [SemperDiscere](https://github.com/SemperDiscere)

## Description
This is a modification of Klicky probe to be used with a Dragon UHF (Ultra High Flow) with the UHF Extesion on a standard Dragon Mount.  It's only Klicky (no NG or UnKlicky planned, feel free to expand).  The Dragon UHF (57mm) is 17mm longer (without nozzles) than the DragonSF/HF (40mm). The Probe point is dropped 17mm to accomodate the Volcano style heater and UHF extension.

## Build
Build Is Similar to the AB Mount. 
- Solder wires to the outside pins of the D5F-L switch
- Remove Lever from switch
- Estimate wire length and cut
- Strip Wires
- Feed wires through Holes
- Seat Magnets
- Test continuity
- Trim wires
- Screw switch to Main Body

Klicky probe Front

Klicky probe 3/4

Klicky probe Rear

Klicky probe Wires
## Source Klicky probe file
[Klicky Probe](../../CAD/KlickyProbe_v2_v59.step)

## Changelog
v0 23/08/2022 SemperDiscere's Dragon UHF Probe Initital

## Model:
| No | Name | Printable |
| -- | --- | --- |
| 1  | Dragon UHF Probe STL | [Yes](../stl/Klicky_Probe_Dragon_UHF v0.stl) |
| 1  | Dragon UHF Probe 3MF | [Yes](../stl/Klicky_Probe_Dragon_UHF v0.3mf) |

## CAD formats:
| No | Name | Printable |
| -- | --- | --- |
| 1  | Dragon UHF Probe F3D | [Yes](../cad/Klicky_Probe_Dragon_UHF v0.f3d) |
| 1  | Dragon UHF Probe STEP | [Yes](../cad/Klicky_Probe_Dragon_UHF v0.step) |

## BOM:
| Qty | Name | Observations |
| --- | --- | --- |
| 4 | 6x3 Magnets | Neodymium preferred |
| 2 | M2 10mm | carpentry type |
| 2 | 5cm 24 ga wire | FEP or PTFE preferred |
| 1 | Omron D2F-5 switch | remove lever if present |

## Hardware Required 
Voron (or printer that uses a voron probe) + Standard Dragon Mount + Dragon UHF Hotend

## To Do 
better pictures

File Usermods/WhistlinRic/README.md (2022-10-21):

A mod to change the print orientation for UnKlickyNG BFG.

Prints in two halves joined by an m2x10 and the m3x14 (or m3x12) used for the
probe.

The pin also retains the magnet, it's a single wall thickness so your mileage
may vary.

The top-hat just seemed a little flimsy when I printed it.

UnKlickyNG BFG M2

discord: whistlinric
github: richardjm

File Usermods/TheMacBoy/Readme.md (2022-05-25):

---
title: TheMacBoy's Klicky Probe mount for EVA and Ender 5 Plus (with rails) compatibility
---

> Created by: [TheMacBoy](https://github.com/themacboy)

## Description
This is a modification of Klicky probe to be used in the EVA carriage, plus support arm for Ender 5 Plus with rails.

Klicky probe right

Klicky probe left

Klicky probe bottom

Klicky probe inside

Klicky probe

Ender 5 Plus support arm front

Ender 5 Plus support arm

## Compatible EVA version
2.2.0 - ?

## Related EVA parts
universal_face

## Source Klicky probe files
[Klicky Probe](../../Probes/KlickyProbes/STL)

## Source OnShape files
[Klicky mount for Eva ](https://cad.onshape.com/documents/2fc54d83c144f64dfbd5b70d/w/5a27aacdedad8aa85274c7e9/e/03e92f0ea05a500c94d12e60)

## Source FreeCad files
Ender-5 Plus arm support inside cad folder

## Changelog
v0.5 30/12/2021 TheMacBoy Release

v0.6 09/01/2022 Klicky probe modified the back size of the frame support, new version v.2

16/02/2022 Added my custom "klicky-variables.cfg" macro as example (my custom settings on my custom Ender-5 Plus ;)

## BOM Parts:
| No | Qty | Name | Printable |
| -- | --- | --- | --- |
| 1  | 1 | Eva-2.2 Klicky probe mount | [Yes](EVA_2.2^/stl/eva-2.2-klicky_probe_mount.stl) |
| 1  | 1 | Ender-5 Plus support arm v.1 | [Yes](Ender-5_(pro,plus)/stl/ender_5_plus-arm_v.1-body.stl) |
| 1  | 1 | Ender-5 Plus support arm v.2 | [Yes](Ender-5_(pro,plus)/stl/ender_5_plus-arm_v.2-body.stl) |

## STEP format:
| No | Qty | Name | Printable |
| -- | --- | --- | --- |
| 1  | 1 | Eva-2.2 Klicky probe mount | [Yes](EVA_2.2^/cad/eva-2.2-klicky_probe_mount.step) |
| 1  | 1 | Ender-5 Plus support arm v.1 | [Yes](Ender-5_(pro,plus)/cad/ender_5_plus-arm_v.1-body.step) |
| 1  | 1 | Ender-5 Plus support arm v.2 | [Yes](Ender-5_(pro,plus)/cad/ender_5_plus-arm_v.2-body.step) |

## BOM screws:
| Qty | Name | Observations |
| --- | --- | --- |
| 2 | M3 20mm | (hex head) |
| 1 | M4 20mm | (countersunk head) |
| 1 | M4 10mm | (countersunk head) |
| 2 | M4 T-Nut | |
| 2 | M3 12mm | (hex head) |
| 2 | M3 nuts | |
| 2 | M2 10mm | carpentry type |
| 2 | M3 inserts x D5 x L5 | |

## Hardware Required 
Standard EVA

Ender-5 Plus

## To Do 
pending to draw arm on OnShape

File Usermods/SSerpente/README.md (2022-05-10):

This a collection with all the necessary printed parts to put Klicky probe on VzBot . 
My only personal contribution is the probe dock mount that i made to fit VzBot , all the other parts are not my creation .
I made the probe dock mount with press fit m3 nuts instead of heat inserts used in the original klicky design. 
In case of collision on z axis between the dock and the probe i added 2 more versions : one with z offset of the probe dock mount 1 mm lower and one 1 mm higher .

Klicky probe is a cheap and more precise alternative to various probe sensors (BlTouch, 3dTouch, inductive/capacitive sensors ) , and tested by me a standard deviation of 0.00065 
There are 4 parts needed : probe mount , probe (various probe lengths and even a switch extender if needed can be found on the klicky github) , probe dock and probe dock mount. 
 Inside the pictures folder i will put the print orientation. For the print settings i use a 0.2 layer height, 3 walls,5 top/bottom and 35% infill.

All the credits go to klicky probe creator and obvious to VzBot creators.
Link to VzBot : https://github.com/VzBoT3D/VzBoT-Vz330

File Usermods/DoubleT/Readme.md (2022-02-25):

## Description
This is a modification of Klicky probe to be used in the 2.4 EVA carriage fan duct.

Klicky probe bottom

Klicky probe top

Klicky probe side

Real toolhead image

Real toolhead image

## Compatible EVA version
2.4.0 - ?

## Related EVA parts
back_corexy, Trihorn UHF fan duct

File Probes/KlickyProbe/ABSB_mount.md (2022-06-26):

## AB/SB Mount Assembly

For the AB/SB Mount assembly you need the following parts

- [ ] 3x 6 mm x 3 mm magnets
- [ ] 2 x 18cm 22AWG cable to connect the Klicky Probe to the Microfit Terminal (if it turn out it's too big, can always cut to lenght)
- [ ] Multimeter to check for Continuity 
- [ ] Super Glue

The probe mount wires are also connected with pressure from the magnets, you can use the probe magnets as a template to insert the probe mount magnets, it is easier that way, so that the magnets are not inserted the wrong way.

|  |  |  |  |  |
| :---: | :---: | :---: | :---: | :---: |

You will not lose Y travel on any configuration in the tests that were done.

After everything is assembled let's check again for continuity.



### Press-fit the magnets

You can now press fit the magnets in place:

<p float="left">
  
  
</p>

Insert the AB mount and probe in the helper parts and you can then press fit with a vice or on a hard surface.

<p float="left">
  
  
  
</p>

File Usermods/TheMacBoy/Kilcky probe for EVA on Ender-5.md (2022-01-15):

---
title: TheMacBoy's Klicky Probe mount for EVA and Ender 5 Plus (with rails) compatibility
---

> Created by: [TheMacBoy](https://github.com/themacboy)

## Description
This is a modification of Klicky probe to be used in the EVA carriage, plus support arm for Ender 5 Plus with rails.

Klicky probe right

Klicky probe left

Klicky probe bottom

Klicky probe inside

Klicky probe

Ender 5 Plus support arm front

Ender 5 Plus support arm

## Compatible EVA version
2.2.0 - ?

## Related EVA parts
universal_face

## Source Klicky probe files
[Klicky Probe](../../Base_STL)

## Source OnShape files
[Klicky mount for Eva ](https://cad.onshape.com/documents/2fc54d83c144f64dfbd5b70d/w/5a27aacdedad8aa85274c7e9/e/03e92f0ea05a500c94d12e60)

## Source FreeCad files
Ender-5 Plus arm support inside cad folder

## Changelog
v0.5 30/12/2021 TheMacBoy Release
v0.6 09/01/2021 Klicky probe modified the back size of the frame support, new version v.2

## BOM Parts:
| No | Qty | Name | Printable |
| -- | --- | --- | --- |
| 1  | 1 | Eva-2.2 Klicky probe mount | [Yes](EVA_2.2^/stl/eva-2.2-klicky_probe_mount.stl) |
| 1  | 1 | Ender-5 Plus support arm v.1 | [Yes](Ender-5_(pro,plus)/stl/ender_5_plus-arm_v.1-body.stl) |
| 1  | 1 | Ender-5 Plus support arm v.2 | [Yes](Ender-5_(pro,plus)/stl/ender_5_plus-arm_v.2-body.stl) |

## STEP format:
| No | Qty | Name | Printable |
| -- | --- | --- | --- |
| 1  | 1 | Eva-2.2 Klicky probe mount | [Yes](EVA_2.2^/cad/eva-2.2-klicky_probe_mount.step) |
| 1  | 1 | Ender-5 Plus support arm v.1 | [Yes](Ender-5_(pro,plus)/cad/ender_5_plus-arm_v.1-body.step) |
| 1  | 1 | Ender-5 Plus support arm v.2 | [Yes](Ender-5_(pro,plus)/cad/ender_5_plus-arm_v.2-body.step) |

## BOM screws:
| Qty | Name | Observations |
| --- | --- | --- |
| 2 | M3 20mm | (hex head) |
| 1 | M4 20mm | (countersunk head) |
| 1 | M4 10mm | (countersunk head) |
| 2 | M4 T-Nut | |
| 2 | M3 12mm | (hex head) |
| 2 | M3 nuts | |
| 2 | M2 10mm | carpentry type |
| 2 | M3 inserts x D5 x L5 | |

## Hardware Required 
Standard EVA

Ender-5 Plus

## To Do 
pending to draw arm on OnShape

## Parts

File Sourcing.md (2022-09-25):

# Trusted suppliers

The following shops are all responsive and helpful, they can help with the sourcing of the required parts for your klicky probe.

| **Shop** |  **Location** | Hadware Kits | Parts | Klicky printed parts | Comments |
| --- | :---: | :---: | :---: | :---: | --- |
| [Fabrekko](https://www.fabreeko.com) | :us: | :heavy_check_mark: | some | :x: | lots of parts to expand 3d printers |
| [Lab4450](https://lab4450.com/) | :eu: :portugal: | :heavy_check_mark: | :x: |  :heavy_check_mark:  | kits for V0, V2, VT, Switchwire, Vcore, PCB's |
| [Vonwange](https://vonwange.com/) | :eu: :de: | :heavy_check_mark: | :heavy_check_mark: |  :heavy_check_mark:  | lots of parts to expand 3d printers |
| [Replimat](https://www.replimat.eu)  | :eu: :de: | :heavy_check_mark: | :heavy_check_mark: | :x: | specializes in some hard to find items |
| [KB-3D](https://kb-3d.com) | :us: | :heavy_check_mark: | :heavy_check_mark: | :x: | specializes in Open source community builds and parts|
| [DFH](https://dfh.fm/) | :us: | :heavy_check_mark: | :heavy_check_mark: | :x: | "shit you don't need, at prices you can't afford"|
| [West3D](https://west3d.com/) | :us: | :heavy_check_mark: | :heavy_check_mark: | :x: | "We help you turn your ideas into reality"|

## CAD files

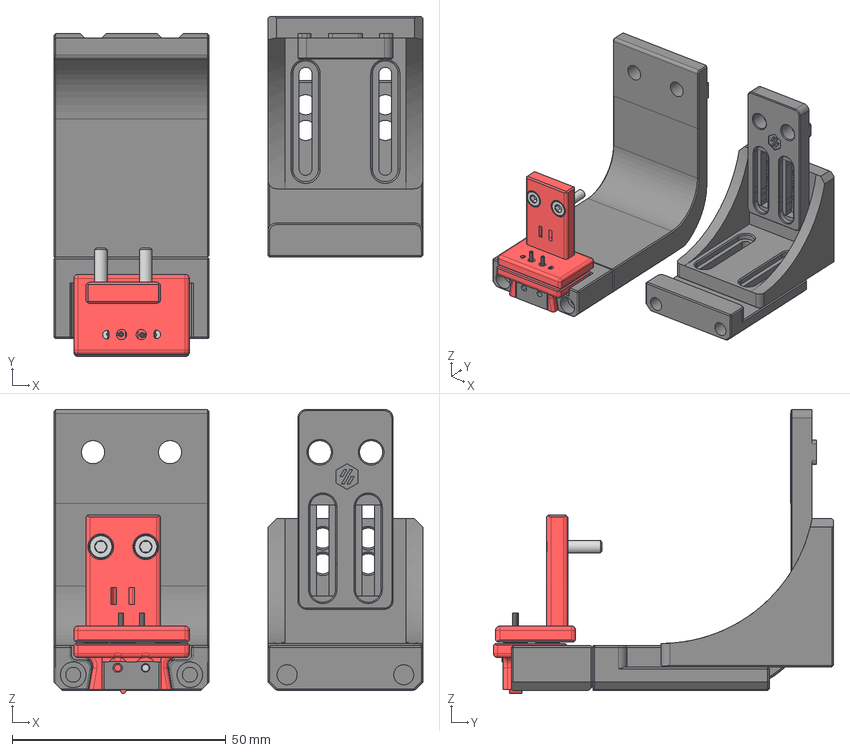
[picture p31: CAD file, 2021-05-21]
CAD/KlickyProbe.step
86.3 x 79.5 x 66.4 mm
M3x10 SHCS x 2
3x6mm Magnet x 3
Isolator
Conductor
Isolator (1)
Conductor (1)
D2F_BASE (1)
D2F_ACTUATOR (1)
3x6mm Magnet (1)
3x6mm Magnet (2)
3x6mm Magnet (3)
3x6mm Magnet (4)
M3x20 SHCS x 2
3x6mm Magnet (5)
M3x8 SHCS (1) x 8
M3 Threaded Insert (1) x 2
M3 Threaded Insert x 2

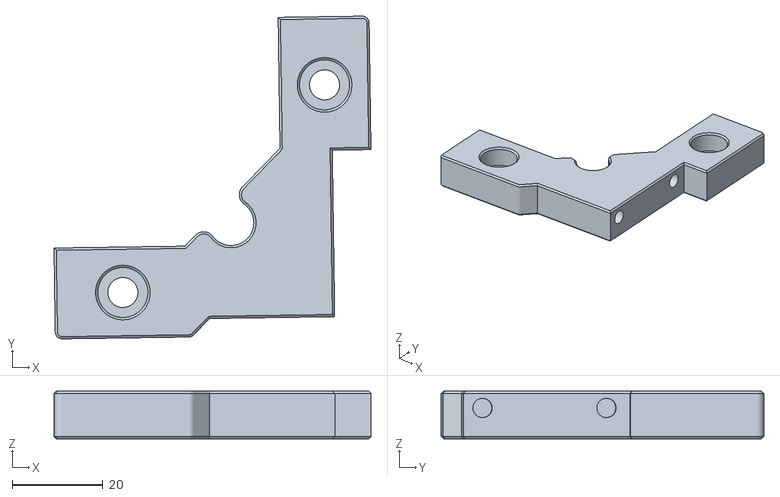
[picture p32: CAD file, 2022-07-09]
Printers/Ratrig/VCore3.0_3.1/VCore3_STL/Vcore3_Dock_mount.stl
69.7 x 71.0 x 10.5

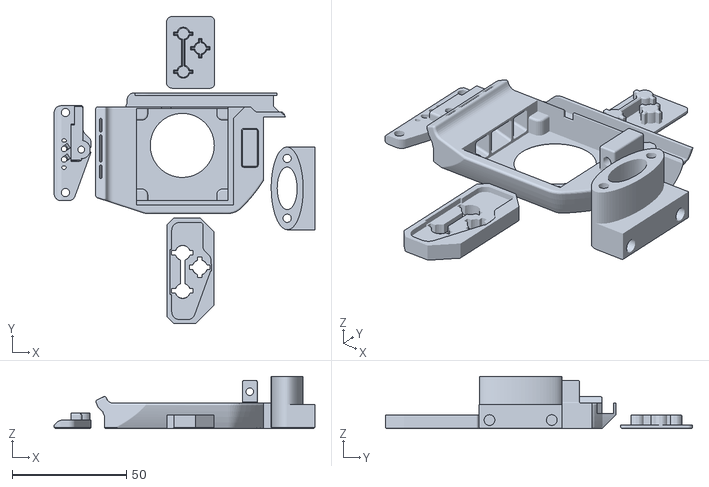
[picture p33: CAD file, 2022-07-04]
Printers/Tiny-M/STL/Tiny-M_STL.stl
114.0 x 134.3 x 22.8

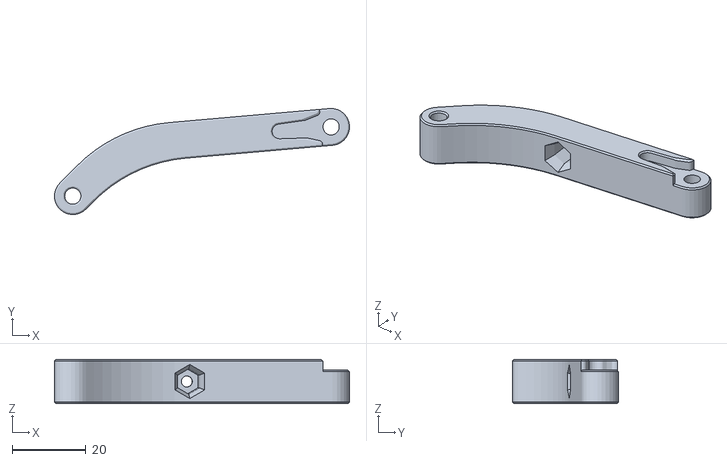
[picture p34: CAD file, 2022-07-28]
Printers/Voron/Switchwire/SW_STL/Drive_arm_front.stl
80.0 x 28.7 x 12.0

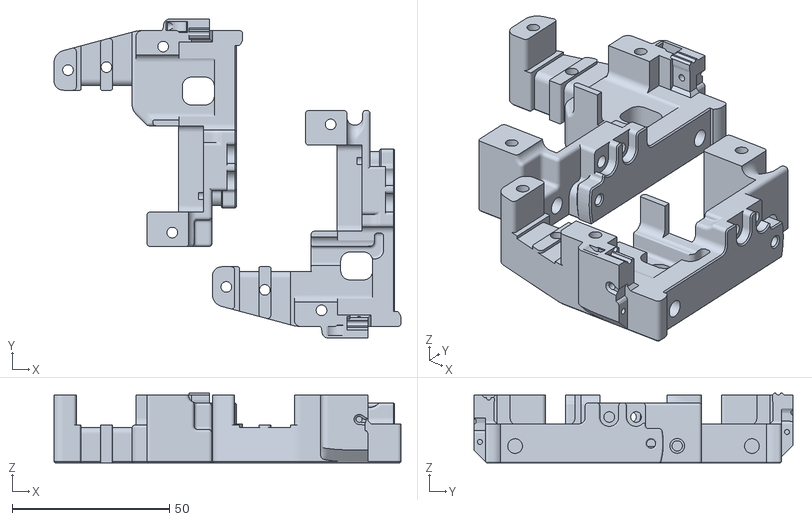
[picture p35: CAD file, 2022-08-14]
Printers/Voron/Switchwire/Usermods/JosAr/SW_X_Carriage_CW2_KlickyNG/SW_X_Carriage_CW2_KlickyNG.stl
110.4 x 101.7 x 22.2

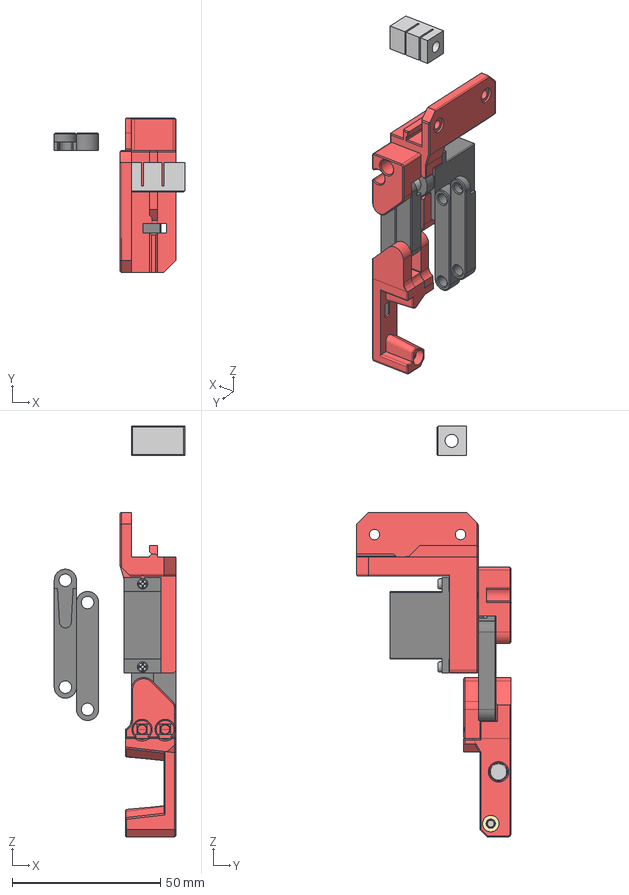
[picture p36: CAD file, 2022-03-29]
Printers/Voron/v0/Usermods/KlickSwipe/CAD/KlickSwipe.step
44.0 x 52.1 x 138.5 mm
Tube Cutting Jig
Free Arm - 22mm
Free Arm - 32mm
Drive Arm - 22mm
Drive Arm - 32mm
Servo Mount Top
6mm x 3mm Round Neodymium Magnet
M3x12 BHCS
M3 Threaded Insert x 5
Klicky Dock Bottom
Servo Mount Body
Servo Arm
M3x8 BHCS x 4
4mm x 14mm PTFE Tube x 3
4mm x 7mm PTFE Tube
M2 Self Tapping Screw x 2

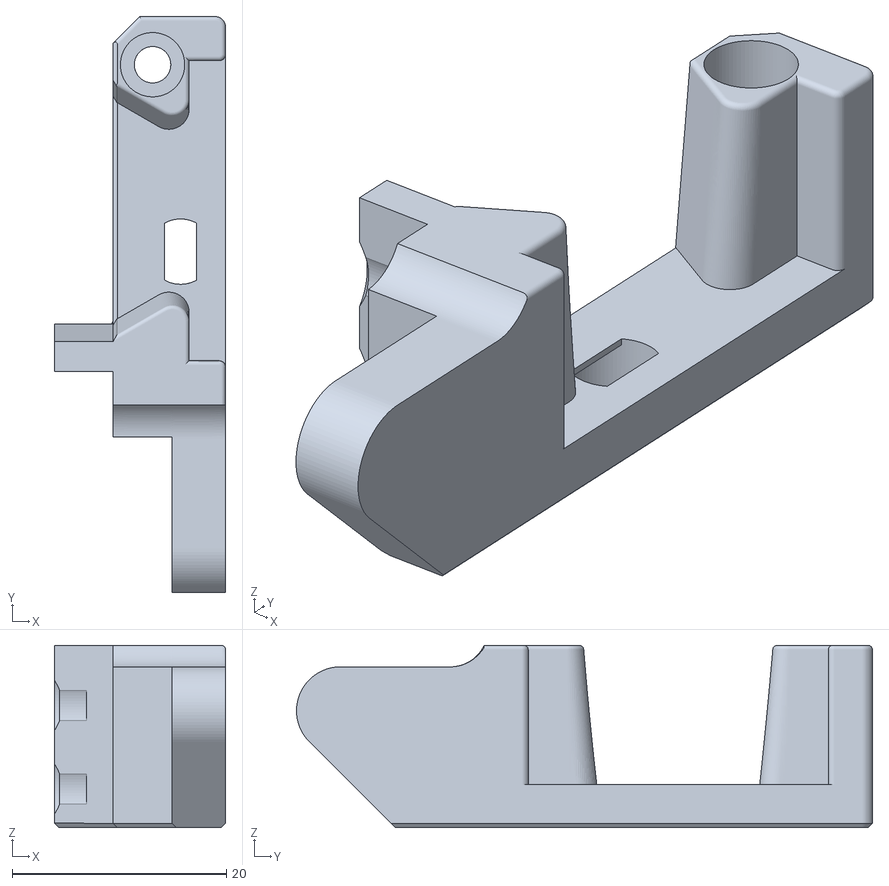
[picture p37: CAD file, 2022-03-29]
Printers/Voron/v0/Usermods/KlickSwipe/STL/[a]_klicky_dock_x1.stl
16.0 x 53.8 x 17.0

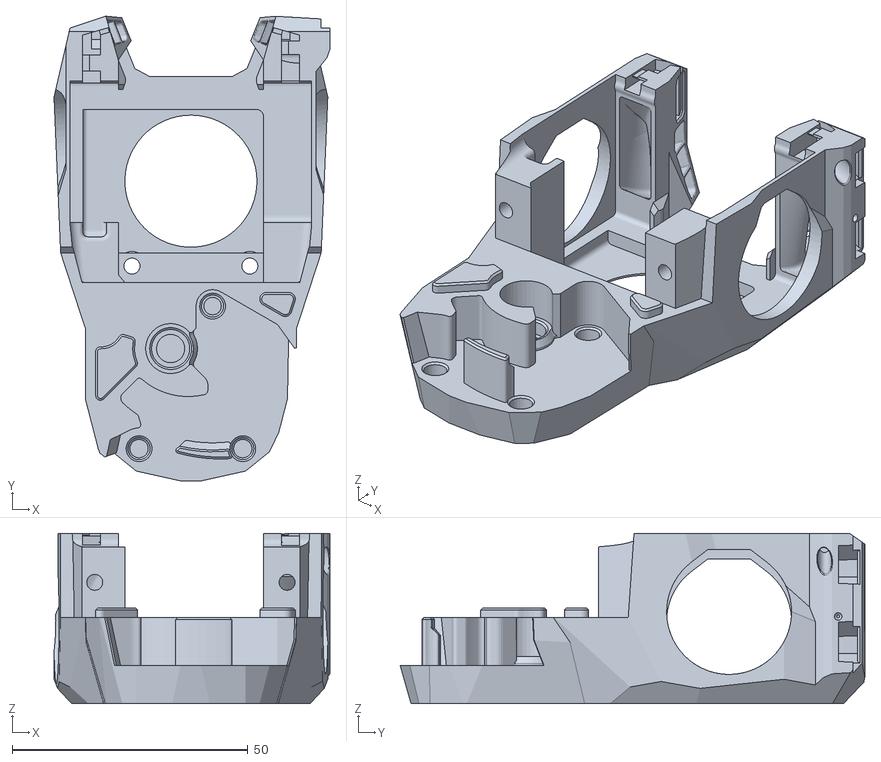
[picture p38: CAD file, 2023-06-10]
Printers/Voron/v0/v0_STL/V0.2r1_KlickyNG_MiniSB_Cowling.stl
58.5 x 98.6 x 36.1

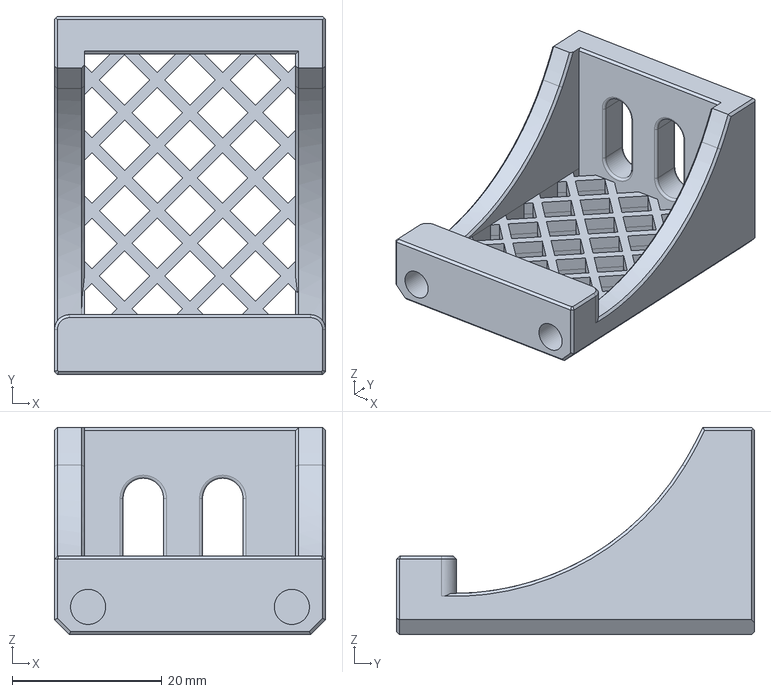
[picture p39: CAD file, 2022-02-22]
Printers/ZeroG/Mercury_One/Voron_Toolhead_CAD/Dock_mount_Ender5.step
36.3 x 47.9 x 27.7 mm

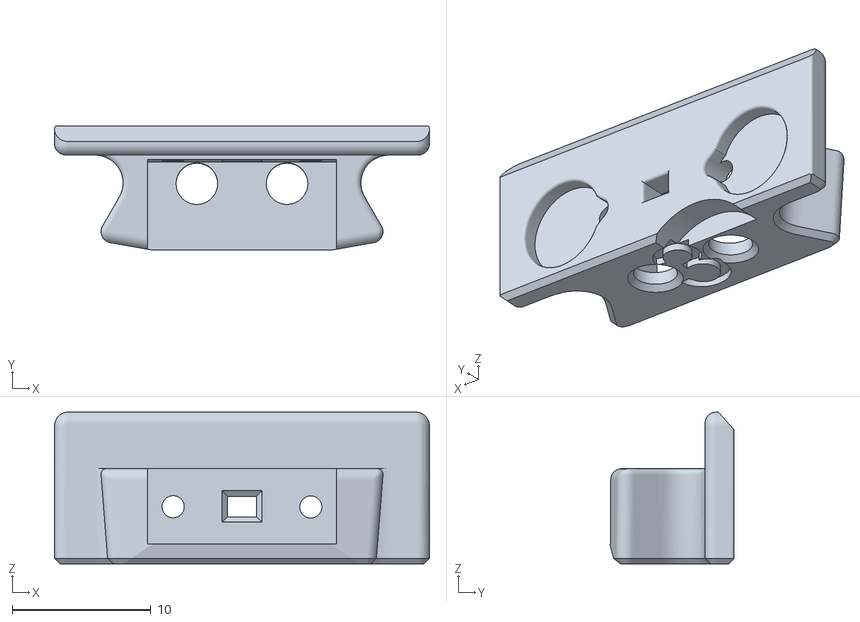
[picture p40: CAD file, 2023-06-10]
Probes/KlickyNG/STL/KlickyNG_Probe_insert_3mm.stl
27.0 x 8.97 x 10.9

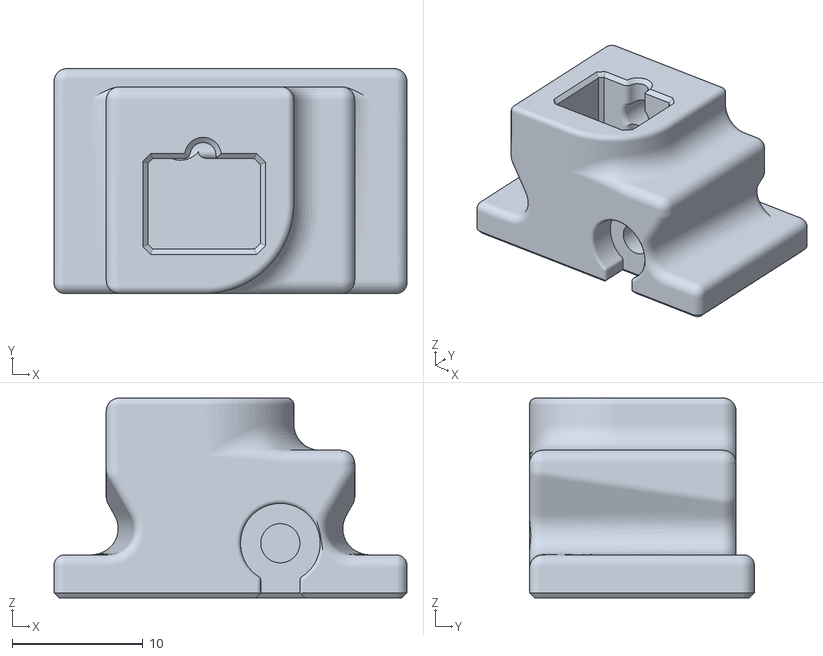
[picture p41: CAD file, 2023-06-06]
Probes/KlickyProbe/STL/BFP Unklicky Body.stl
27.0 x 17.2 x 15.3

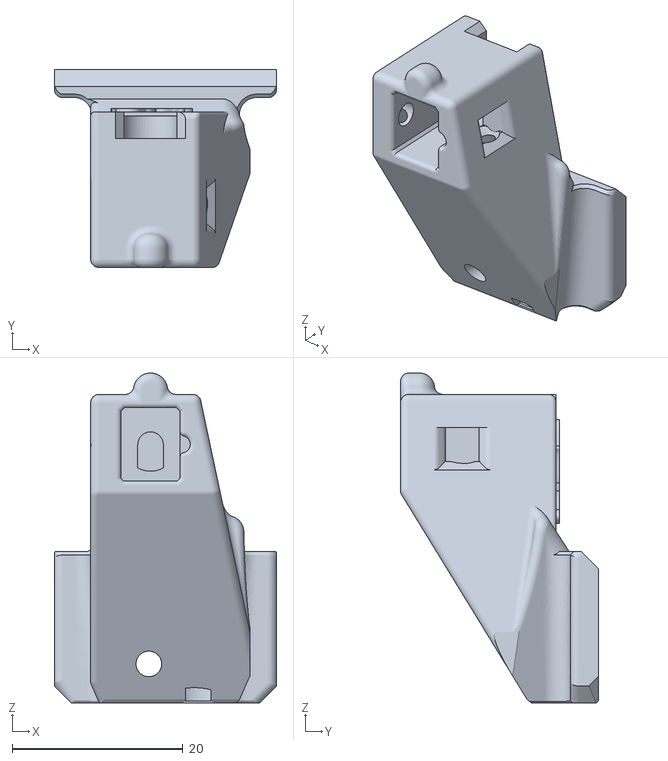
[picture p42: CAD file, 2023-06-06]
Probes/Unklicky/STL/KP_Unklicky_Long_Tm_body.stl
26.0 x 23.2 x 38.6

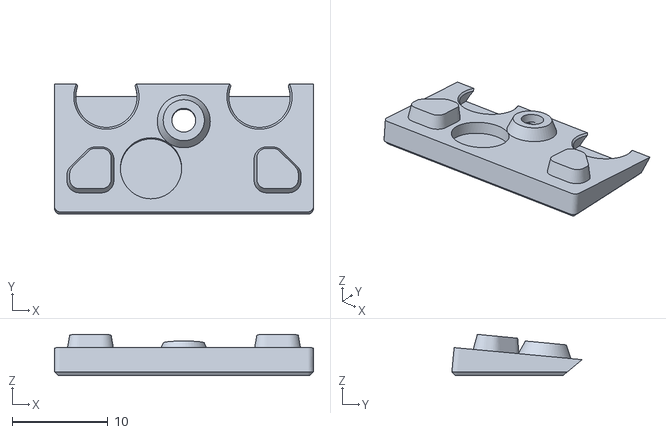
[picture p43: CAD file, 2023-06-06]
Probes/UnklickyNG/STL/KlickyNG_Cap_2_7mm.stl
27.0 x 13.6 x 4.31

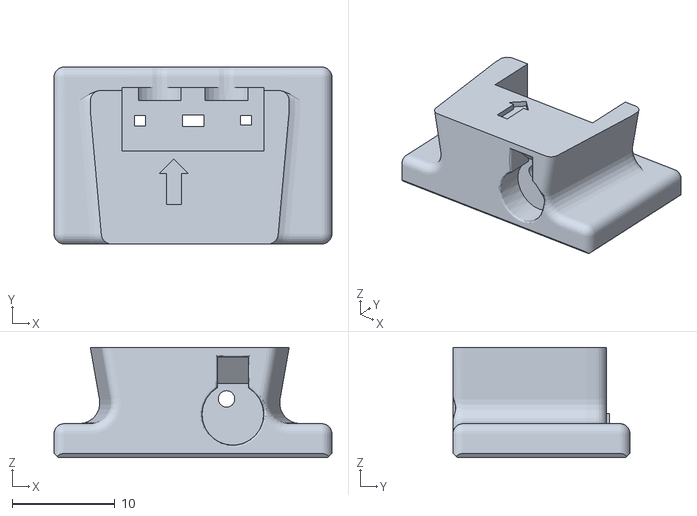
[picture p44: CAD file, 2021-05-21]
STL/KlickyProbe Probe.stl
27.0 x 17.2 x 10.7

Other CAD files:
Usermods/DoubleT/CAD/Klicky_-_Eva_2.4_mount.step
Usermods/DoubleT/Stl/Klickymount_EVA_fanduct.stl
Usermods/JarTheHead/CAD/Klicky_Probe_RtV6 v0.step
Usermods/JarTheHead/STL/ProbeRtV6.stl
Printers/Ratrig/VCore3.0_3.1/VCore3_STL/EVA2_Klicky_mount.stl
Printers/Ratrig/VCore3.0_3.1/VCore3_STL/EVA3 Klicky Mount.stl
Printers/Ratrig/VCore3.0_3.1/VCore3_STL/Vcore3_Klicky_Piston.stl
Printers/Ratrig/VCore3.0_3.1/VCore3_STL/Vcore3_Klicky_Piston_body.stl
Printers/Voron/Switchwire/SW_STL/2mm_extender.stl
Printers/Voron/Switchwire/SW_STL/Drive_arm_back.stl
Printers/Voron/Switchwire/SW_STL/KlickyProbe_AB_mount_v2.stl
Printers/Voron/Switchwire/SW_STL/Mount_magnet_holder.stl
Printers/Voron/Switchwire/SW_STL/Mount_magnet_pressfit_helper.stl
Printers/Voron/Switchwire/SW_STL/Mount_pressfit_holder.stl
Printers/Voron/Switchwire/SW_STL/Servo_Mount_Body_center.stl
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

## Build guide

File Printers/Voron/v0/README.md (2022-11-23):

# Klicky Probe for  Vorondesign v0 printers

Here you will find the necessary files and documentation to print and setup your own klicky probe on the v0 (and v0.1)

This directory has the STL files properly oriented for printing and community mods for the respective printer, there are [klipper](../../../Klipper_macros) macros and [RRF](../../../RRF_macros) macros on the repository.

You can find more information about the Voron printers at the [website](https://vorondesign.com/) or go check the [discord](https://discord.gg/voron), for the record, i own a v2.4, this is how i would describe them "A Voron is a fast high quality printer, i print with much better quality  the perimeters at the draft speed of my old bedslinger. It also has a  big community with lots of documentation and new ideas."

With an integrated mount, the bed can be fully used during printing, the bed only cannot be probed (at most) 6mm on the left side, this is due to the design of the probe, that extends below the nozzle.

There are currently two other probes available to use on the V0.1, Slideswipe and Sideswipe.

Above all, have fun and be excellent to one another, now to the instructions.

**Note that there's KlickyNG CAD and STL files already on the repository, these instructions need to be updated to reflect that, please [check the various probe assembly options](../../../Probes	)**.with some variance, with the V0 instructions you should be able to piece together what is missing. 

This mod is not yet on [VoronUsers repository](https://github.com/VoronDesign/VoronUsers/tree/master/printer_mods/JosAr/Klicky-Probe), should be soon. 

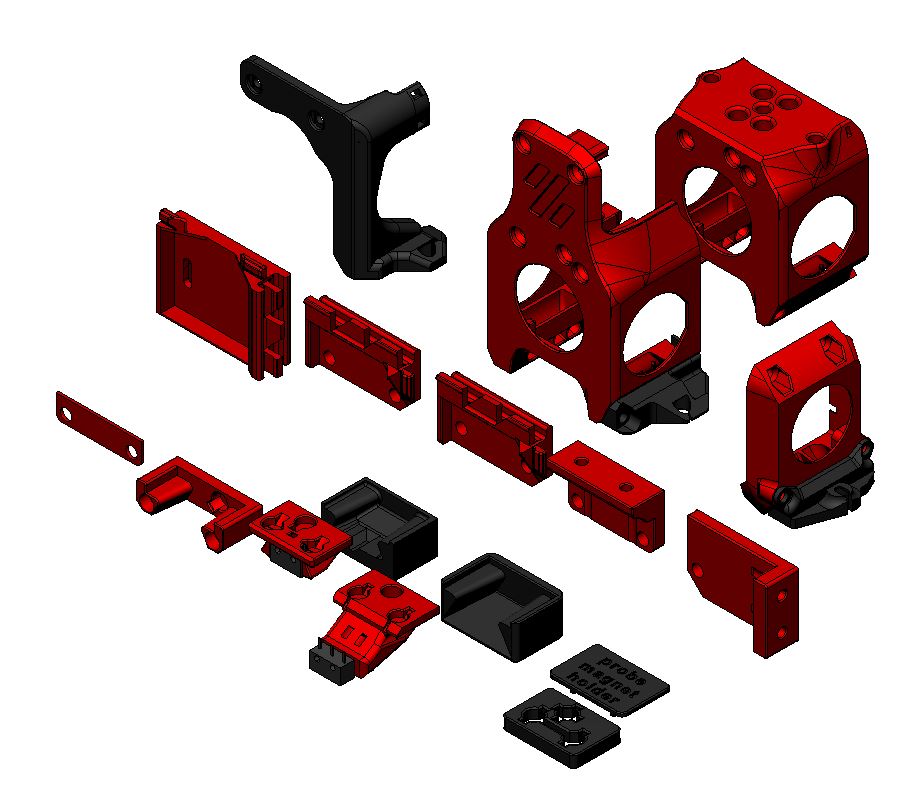
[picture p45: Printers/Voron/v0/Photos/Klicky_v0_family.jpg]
V2.4 Klicky Probe


## Mounting options

### Probe dock mount

The probe dock is mounted to the front right extrusion, where it minimizes the chance of being removed inadvertently during printing, like this:

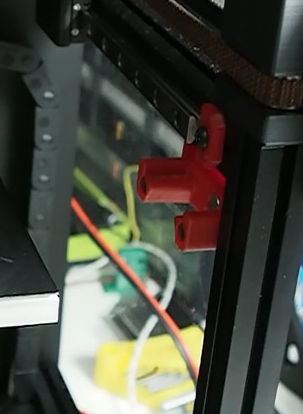
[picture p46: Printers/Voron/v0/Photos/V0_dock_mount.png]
Klicky Dockmount attached


There are several mounting options, depending on your setup:

It can be frustrating on the v0 to add extra m3 nuts on the 1515 extrusion after the assembly is complete, so there are several screwless probe dock options to avoid that scenario.

| Screwless variable | Fixed | Fixed extrabeef | Top screws | Side screws |
| :---: | :---: | :---: | :---: | :---: |
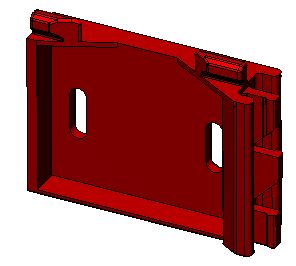
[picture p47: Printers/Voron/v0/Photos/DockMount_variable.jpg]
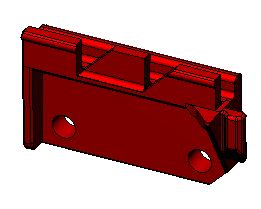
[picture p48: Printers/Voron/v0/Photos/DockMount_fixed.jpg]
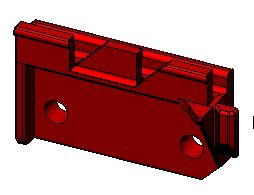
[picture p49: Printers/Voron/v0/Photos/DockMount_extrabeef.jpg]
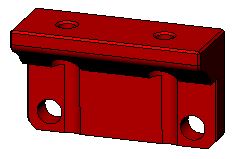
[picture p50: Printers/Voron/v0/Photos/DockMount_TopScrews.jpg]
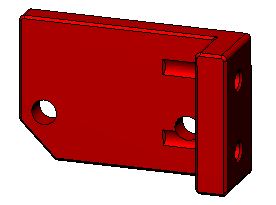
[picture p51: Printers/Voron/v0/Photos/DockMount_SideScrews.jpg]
|  |  |  |  |  |
| recommended for most setups, does not require extra m3 nuts on the extrusion (v0.0/1) | fixed position, does not require extra m3 nuts on the extrusion (v0.1) | fixed, fits X carriages that are 2mm thicker, does not require extra m3 nuts on the extrusion(v0.1) | fixed, requires 2 extra m3 nuts on the top extrusion (v0.1) | fixed, requires 2 extra m3 nuts on the front extrusion (v0.1) |

There are also some more mounting options on [Usermods](./Usermods/), like a servo powered dock. ***Check it out***

### Probe toolhead mount

The v0 toolhead was not designed to use a probe, so there is no inbuilt location to add one, so i designed two options for the v0.1 variant and one for the original v0.

#### Front cowling mount (v0.1)

You can install a mount the attaches to the front of the toolhead cowling, it will need 2/3mm of X space on the front right of the bed to avoid picking the probe up by accident, it is very easy to install, it's ideal to test the concept of probing on the v0.1

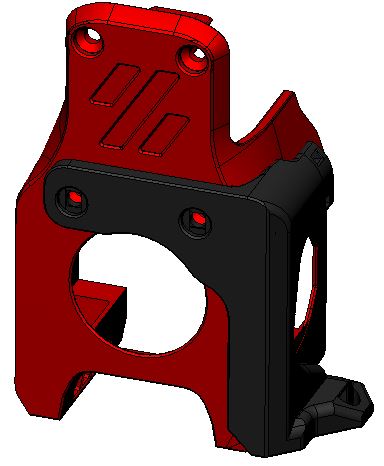
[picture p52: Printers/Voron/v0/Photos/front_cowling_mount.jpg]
Front cowling mount
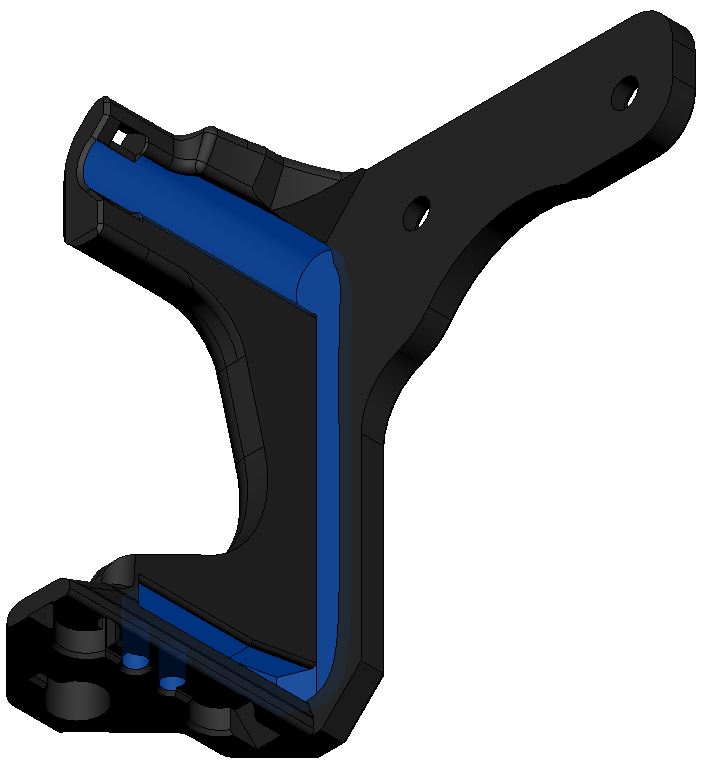
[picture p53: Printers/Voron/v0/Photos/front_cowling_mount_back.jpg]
Front cowling mount
|  |  |
| --- | --- |

You will require 2x M3 x 40mm (BHSC preferably) that are not on the V0(.1) BOM, there is an included wire path with zip tie support, to keep your printer looking good.

#### Integrated cowling (v0.1)

You can replace the cowling with a version that has a cutout to allow the klicky mount to attach, it has no impact on the cooling performance of the probe, it also includes a wire path to the back of the miniAB.

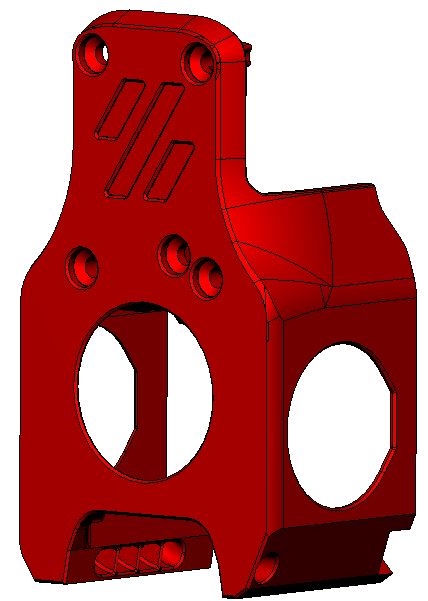
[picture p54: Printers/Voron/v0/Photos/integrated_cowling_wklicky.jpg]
Integrated klicky cowling
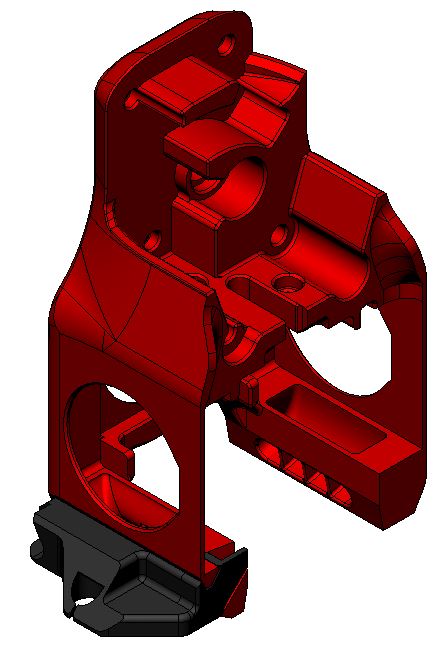
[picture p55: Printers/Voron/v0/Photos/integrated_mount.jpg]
Klicky mount
|  |  |
| --- | --- |

This method allow mounting of different probes on the V0.1, currently only klicky uses this mount, hopefully that can change in the future.

It also allows to pick up the probe at X121, effectively outside the bed, incurring in a no print space lost.

#### Fan duct mount (v0.0)

On the V0.0, you do not need to reprint the entire cowlink, you only need to replace the right fan duct with a version that has a mount for klicky, it has no impact on the cooling performance of the probe, it also includes a wire path to the back of the miniAB.

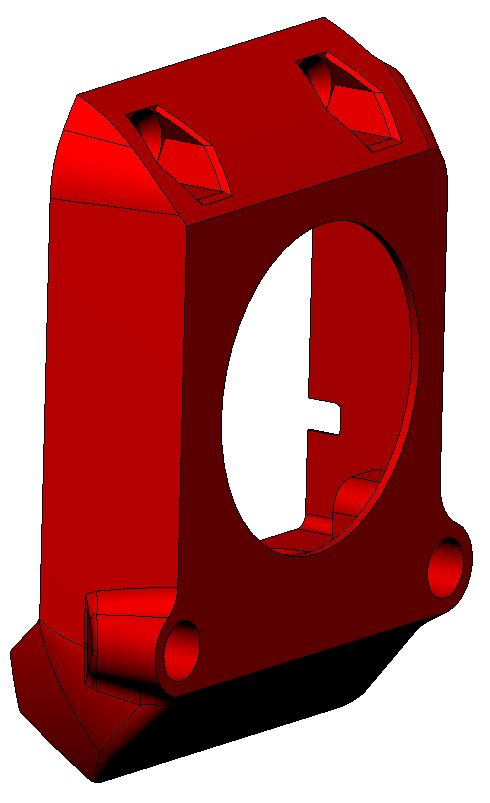
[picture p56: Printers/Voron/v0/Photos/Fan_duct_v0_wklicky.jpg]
V0 fan duct
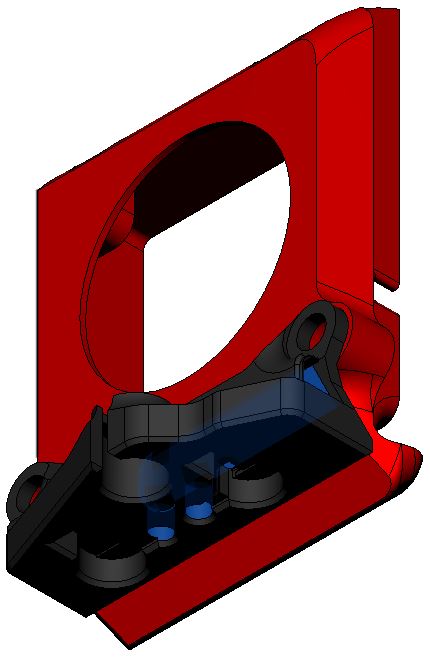
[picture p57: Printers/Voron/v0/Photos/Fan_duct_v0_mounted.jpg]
Klicky
|  |  |
| --- | --- |

This version has seen little tests because of the lack of a sufficient number of v0.0 to test on.

If you end up using this version, please tell me at what X do you dock and attach the probe.

It is also necessary to use the Screwless variable dock mount 

## Bill of Materials (BOM)

### Tools:

- 1.5mm Drill (optional)
- Multimeter to check for Continuity 
- Super Glue (optional)
- Soldering Iron

### Probe:

- 1x microswitch (the omron D2F-5 or D2F-5L (removing the lever is required), other also work with reduced accuracy or repeatability (mostly anecdotal evidence, needs a proper sudy)
- 2x M2x10 mm self tapping
- 10cm of 22AWG cable (to wire the magnets to the switch)
- 5x 6 mm x 3 mm magnets (N35 magnets work)

### Probe mount:

| Front cowling mount (v0.1) | Integrated cowling mount (v0.1) | Fan duct mount (v0.0) |
| --- | --- | --- |
| 4x 6 mm x 3 mm magnets (N35 magnets work) | 4x 6 mm x 3 mm magnets (N35 magnets work) | 4x 6 mm x 3 mm magnets (N35 magnets work) |
| 2x 20cm 22AWG cable (to connect the Klicky Probe to the umbilical termination point) | 2x 20cm 22AWG cable (to connect the Klicky Probe to the umbilical termination point) | 2x 20cm 22AWG cable (to connect the Klicky Probe to the umbilical termination point) |
| two wires to connect the controller to the extruder motor vicinity | two wires to connect the controller to the extruder motor vicinity | two wires to connect the controller to the extruder motor vicinity |
| 2x M3 x 40mm BHSC | 1x M3x6 mm BHSC Screw | 1x M3x6 mm BHSC Screw |
| | 1x M3 threaded insert M3x5 mmx4 mm | 2x M3 threaded insert M3x5 mmx4 mm |

### Probe dock:

- 1x 6 mm x 3 mm magnets (N35 magnets work)
- 2x M3x16 mm

### Probe dock mounts:

| Screwless variable (v0.0/1) | Fixed (v0.1) | Fixed extrabeef (v0.1) | Top screws (v0.1) | Side screws (v0.1) |
| :---: | :---: | :---: | :---: | :---: |
| 2x m3 nut | 2x M3 threaded insert M3x5 mmx4 mm | 2x M3 threaded insert M3x5 mmx4 mm | 2x M3 threaded insert M3x5 mmx4 mm | 2x M3 threaded insert M3x5 mmx4 mm |
| | | | 2x m3x8 mm | 2x m3x8 mm |

## Sourcing

To get the best experience, please consider purchasing from the trusted list of suppliers bellow.

[trusted suppliers list](./Sourcing.md)

## Parts location

The probe STL's are located [here](../../../Probes/KlickyProbe/STL).

The printer specific STL's are located [here](./v0_STL).

The CAD with all the parts are [here](../../../CAD).

## What to print

### Probe 

* 2x KlickyProbe_Long_v2.stl (keeping a spare is always a good idea)

The KlickyProbe_v2.stl is also compatible, but has a different Y offset and cannot probe all the bed.

#### Helpers to pressfit the probe magnet

* Probe_magnet_pressfit_helper.stl

* Probe_magnet_holder.stl

* Longer_probe_pressfit_helper.stl

### Probe mount

| Front cowling mount (v0.1) | Integrated cowling mount (v0.1) | Fan duct mount (v0.0) |
| --- | --- | --- |
| Front_cowling_mount.stl | MiniAB_Dragon_Cowling_wKlicky.stl | V0_Fan_duct_wKlicky.stl |
| v0.1_integrated_mount.stl  | v0.1_integrated_mount.stl | v0_integrated_mount.stl |

There are also other integrated cowlings, check the [STL] folder, namely, the Serpa_Mini_Dragon_Cowling_wKlicky.stl from [Kyrios](https://github.com/KurioHonoo/Mini-AfterSherpa) and the LGX Lite cowling from [Bondtech](https://www.bondtech.se/2021/12/27/voron-v0-1-toolhead-setup-for-lgx-lite/).

### Probe dock

* Probe_Dock_v2.stl

### Probe dock mounts

| Screwless variable (v0.0/1) | Fixed (v0.1) | Fixed extrabeef (v0.1)  | Top screws (v0.1) | Side screws (v0.1) |
| --- | --- | --- | --- | --- |
| DockMount_variable.stl | DockMount_fixed.stl | DockMount_extrabeef.stl | DockMount_TopScrews.stl | DockMount_SideScrews.stl |

### Printing instructions

Recommended printing settings:

* initial layer height:0,24
* layer height: 0.2mm
* bottom/top/perimeters: 4
* infill: more than 23%
* infill type: Cubic
* Thin walls: On

It was tested and printed with ABS, might work on other materials, if you try, let me know how it worked out.

### Typical V0.1 components

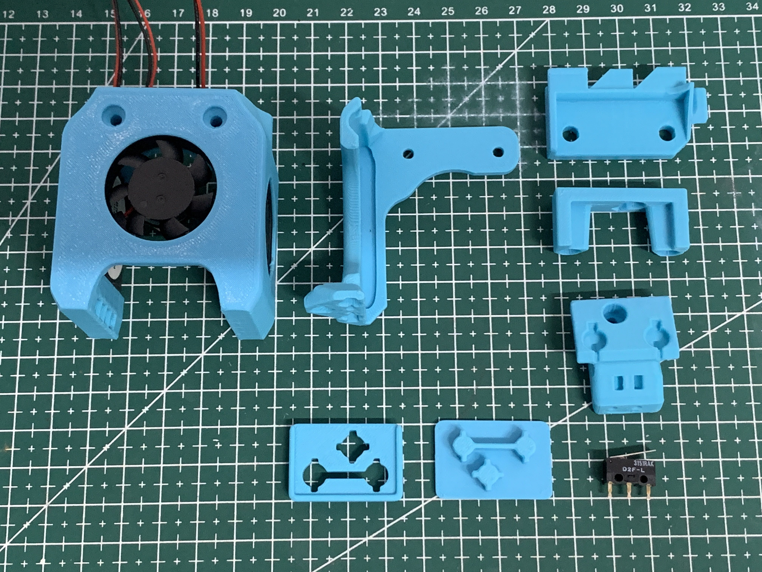
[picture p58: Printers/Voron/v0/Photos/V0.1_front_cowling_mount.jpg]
Klicky v0.1 components


(the images with the green background were provided by user SunB#1489 and are being used with permission).

## Assembly

### Step 1 - Dock mount and Probe Dock assembly 

In this examples, the Fixed dock will be used.

- [ ] 2x M3 threaded insert M3x5 mmx 4 mm
- [ ] 1x 6 mm x 3 mm magnets
- [ ] 2x M3x16 mm
- [ ] Super Glue

Here we will use the Fixed dock as an example, the other docks are very similar.

Install your heat set threaded inserts like you did within your Voron build. 

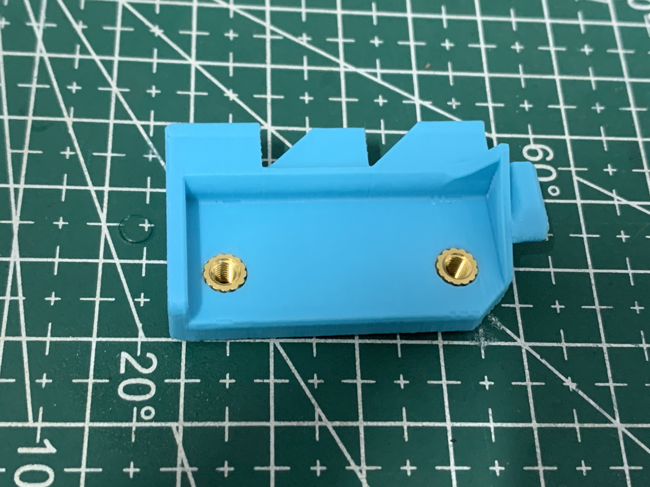
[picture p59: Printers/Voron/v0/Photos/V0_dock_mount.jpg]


Install the magnet in the Probe dock, make sure that the magnet is fully inserted, it's top should be below the plastic.

Screw the dock onto the Dock mount with the two M3x16mm screws.

Secure the magnet with a dab of super glue (not a lot, just a drop).

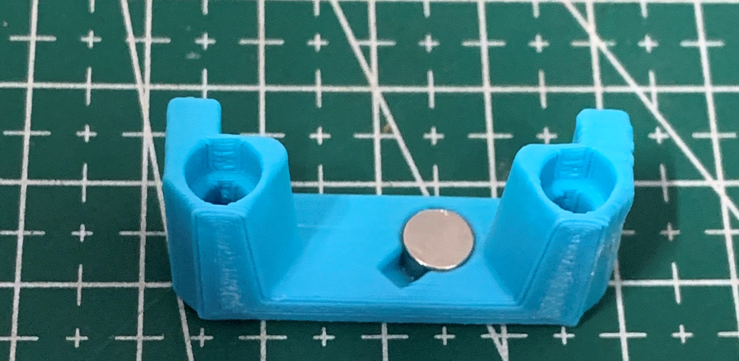
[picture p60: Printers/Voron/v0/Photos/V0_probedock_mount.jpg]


Mount the Probe Dock to the front right extrusion, snap first on the front extrusion, then on the top one (do this after assembling the probe).

Klicky Dockmount attached

### Step 2: Probe Assembly

For the probe assembly you need the following parts:

- [ ] 1x microswitch
- [ ] 2x M2x10 mm self tapping
- [ ] 5x 6 mm x 3 mm magnets
- [ ] 10cm of 22AWG cable
- [ ] 1.5mm Drill (optional)
- [ ] Multimeter to check for Continuity 
- [ ] Super Glue

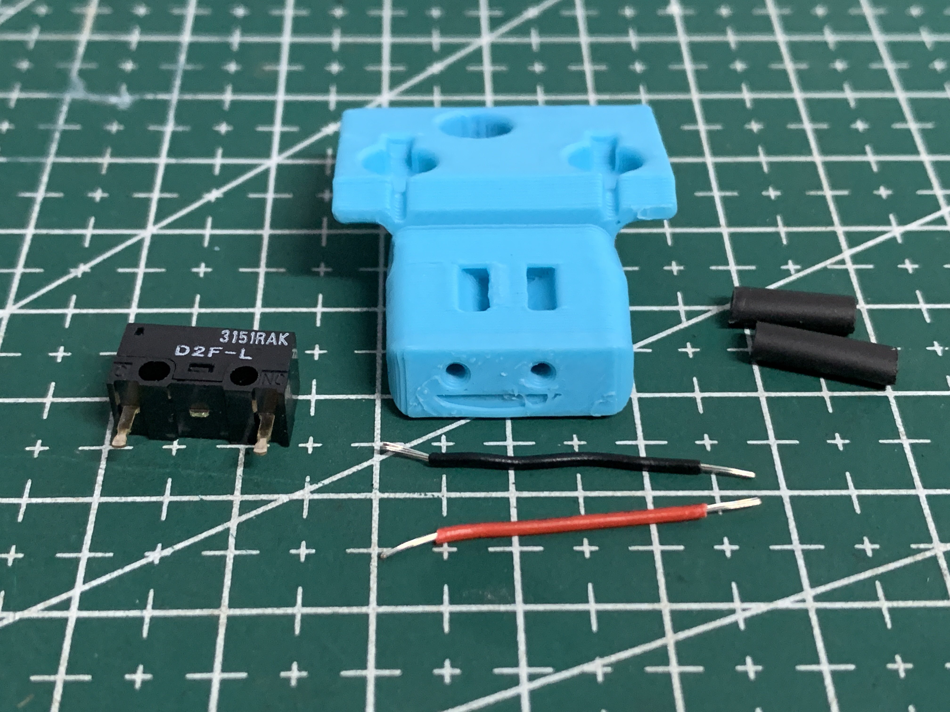
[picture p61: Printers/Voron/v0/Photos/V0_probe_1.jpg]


Maybe you need to clear the holes for the microswitch, a 1.5mm drill bit should work fine.

Install the microswitch so that the arrow on the probe body is pointing to the little switch.

The best way to install the back magnet is to attach a magnet to the probe dock and slide the probe on the dock to insert some distance and the insert he remaining with a tool, it should be slightly below the plastic.

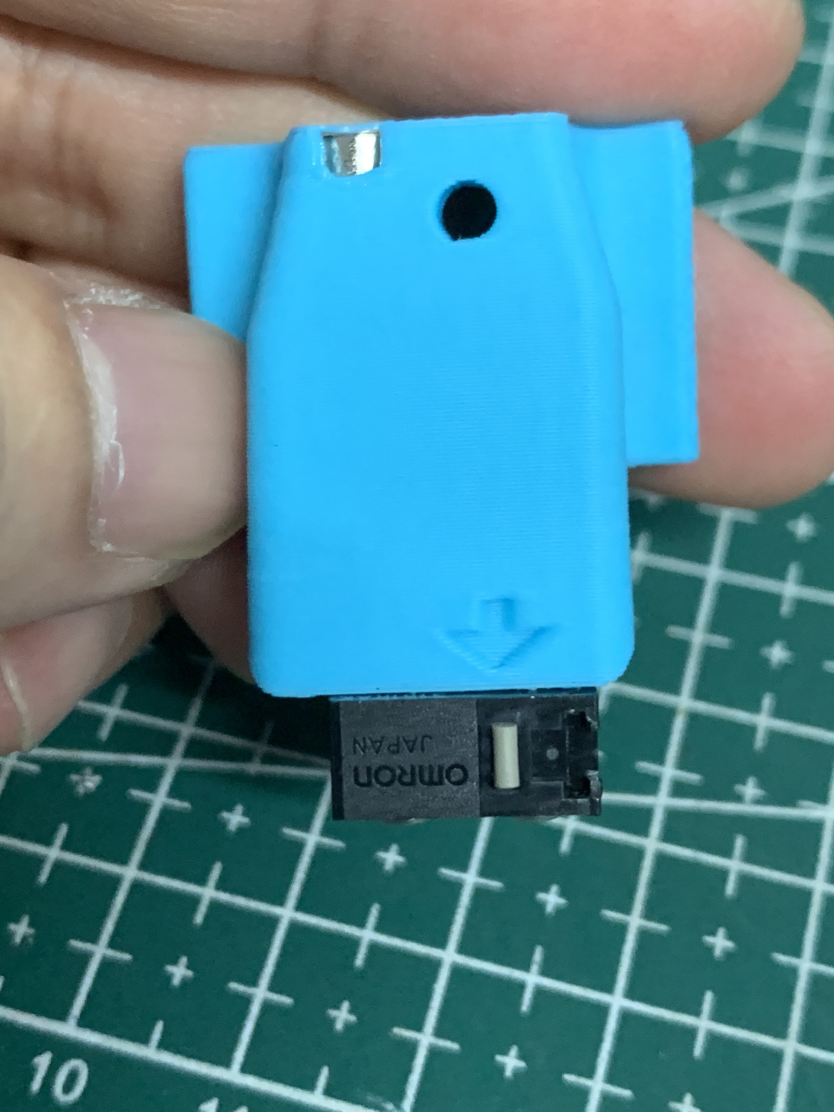
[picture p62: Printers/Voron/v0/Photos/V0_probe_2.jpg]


Then take your self tapping screws and screw the microswitch in place, you should also now solder the wires to the outside pins of the switch, that way making this a Normally Connected probe.

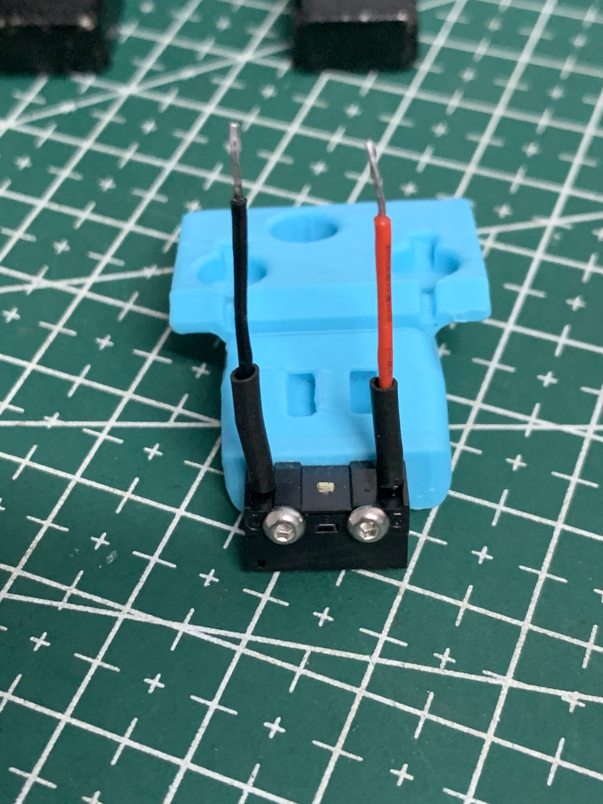
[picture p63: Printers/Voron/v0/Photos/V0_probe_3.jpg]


You should place the wires cover outside the ducts to the magnets and install them in the space below the magnets, more like the right wire is on the image below.

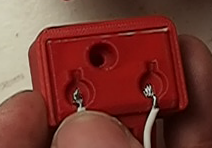
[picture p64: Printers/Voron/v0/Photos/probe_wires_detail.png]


You want to install the magnets in the way that the ones which are connected to the microswitch, have the same polarity.

Before placing the switch magnets, use some super glue on the holes (not a lot, just a drop), avoid the wires and the top of the magnets.

The 3rd magnets (there are two) should have the inverse polarity, wait until the system is complete and assembled before gluing the magnets, they might need adjustment to ensure a good fit on the mount.

You can use the included pressfit helpers to help in securing the probe when you are inserting the magnets.

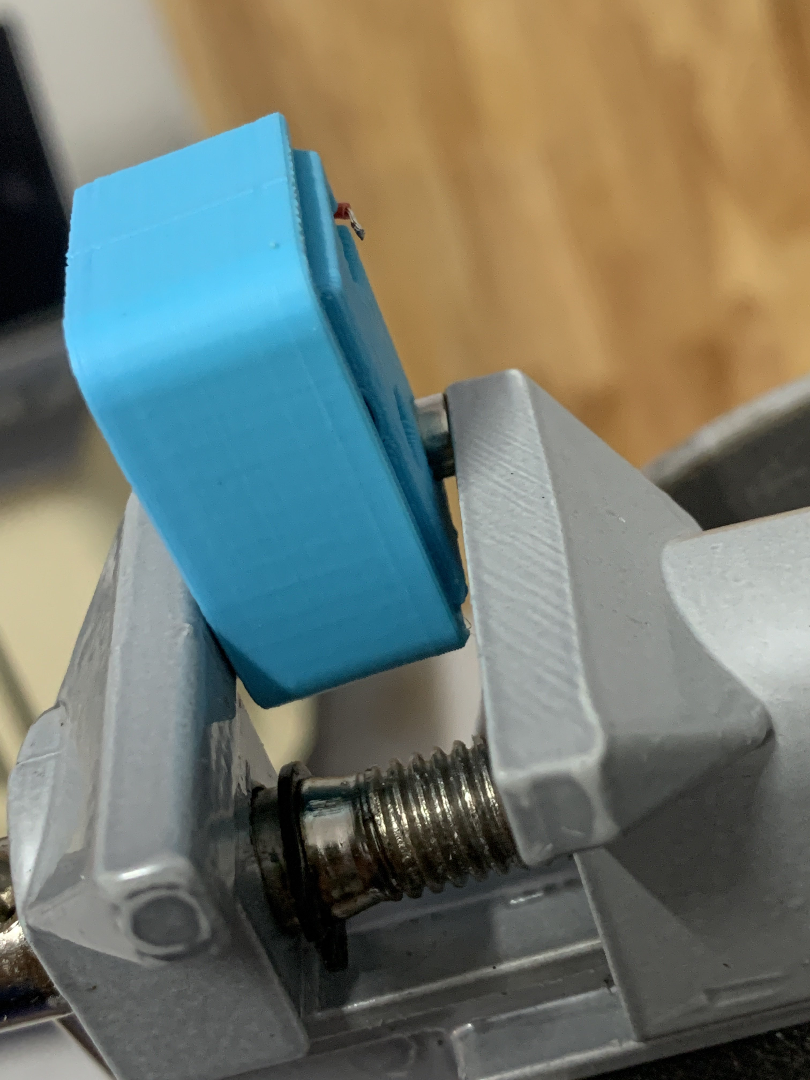
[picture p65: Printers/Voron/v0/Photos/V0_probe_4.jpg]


There is no need for soldering, the probe microswitch connectors are press-fit on the magnets, they should remain with the top above the probe plastic.

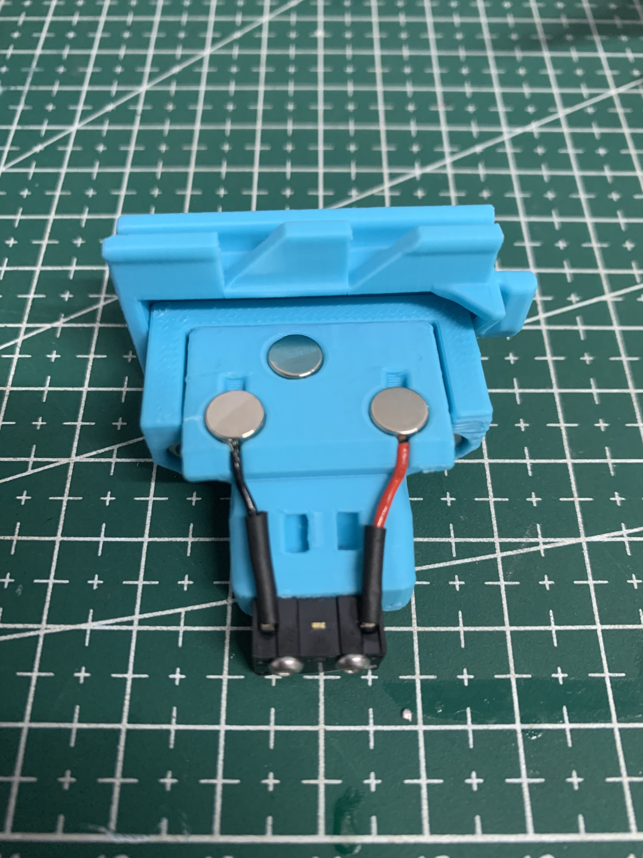
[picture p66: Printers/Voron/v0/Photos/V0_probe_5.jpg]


As the last step of the probe assembly check if you have continuity between two magnets that connect to the switch.

If you have a normally closed switch (as you should), then you should have a current flow, so continuity is established. When you press the switch you should lose continuity. When you have a normally open switch then the behavior is the other way around.

### Step 3: Probe mount Assembly

In this example, the Front cowling mount will be used.

For the Front cowling mount assembly you need the following parts

- [ ] 4x 6 mm x 3 mm magnets
- [ ] 2 x 20cm 22AWG cable to connect the Klicky Probe to the Mircofit Terminal
- [ ] two wires to connect the controller to the extruder motor vicinity
- [ ] some microfit or jst hardware
- [ ] 2x M3 x 40mm BHSC 
- [ ] Multimeter to check for Continuity 
- [ ] Super Glue

The probe mount wires are also connected with pressure from the magnets, you can use the probe magnets as a template to insert the probe mount magnets, it is easier that way, so that the magnets are not inserted the wrong way.

again, before placing the wire magnets, use some super glue on the holes (not a lot, just a drop), avoid the wires and the top of the magnets.

The 3rd magnets (there are two) should have the inverse polarity, exacly like on the probe.

Wait until the system is complete and assembled before gluing the 3rd magnets, they might need adjustment to ensure a good fit on the probe.

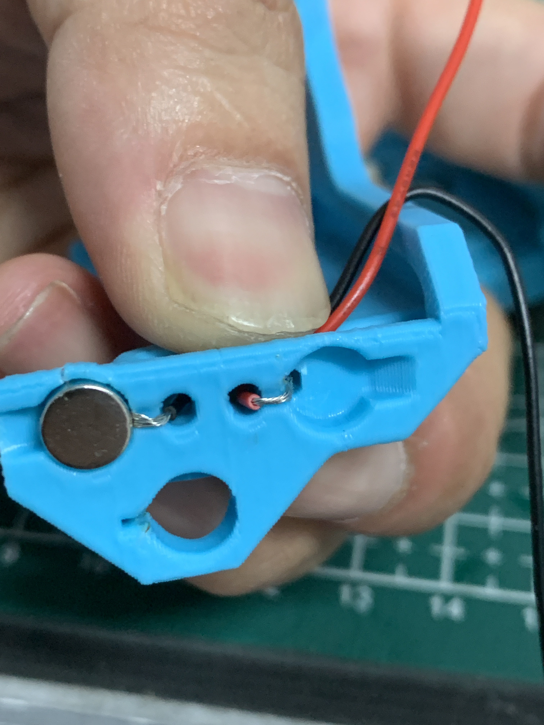
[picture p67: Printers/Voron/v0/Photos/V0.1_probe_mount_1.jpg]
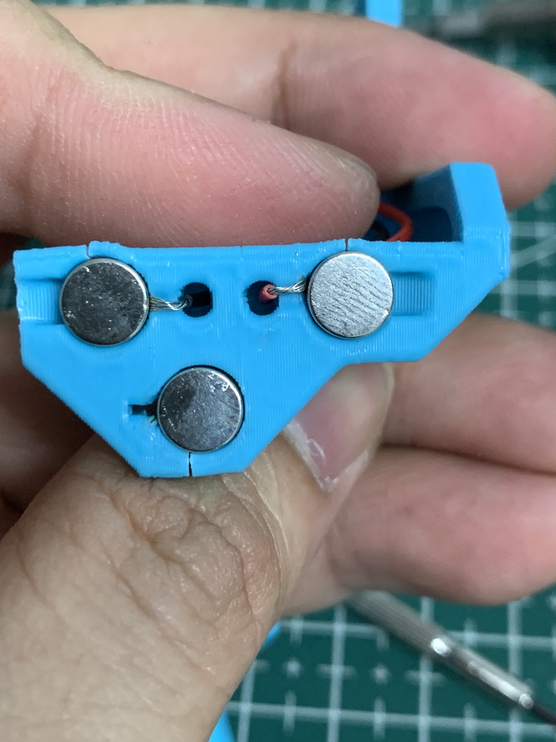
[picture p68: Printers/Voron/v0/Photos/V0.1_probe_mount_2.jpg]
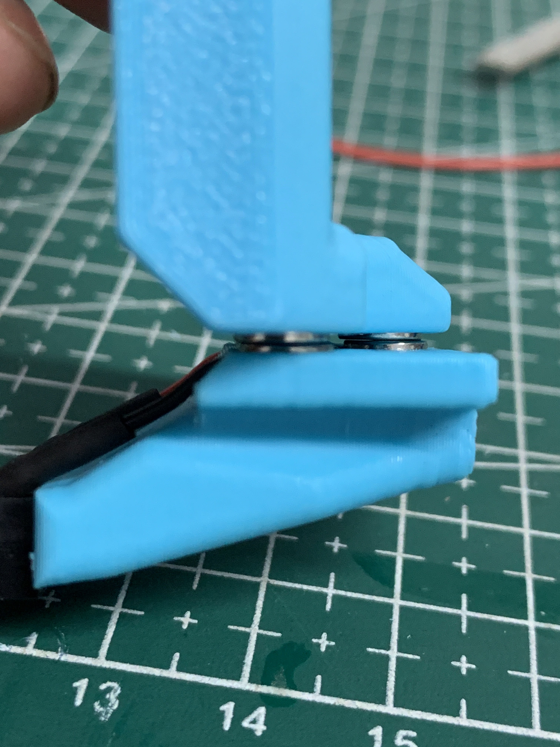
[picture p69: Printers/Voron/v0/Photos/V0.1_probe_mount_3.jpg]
|  |  |  |
| :---: | :---: | --- |

(The mount has since been improved a bit to avoid cracking)

After everything is assembled let's check again for continuity, this time joining the ends of the cable and testing connectivity on the two wire magnets that have a cable.

### Step 4: Probe Mount installation and wiring

For the installation you need the following parts:

- [ ] 2x M3x40 mm BHSC Screws

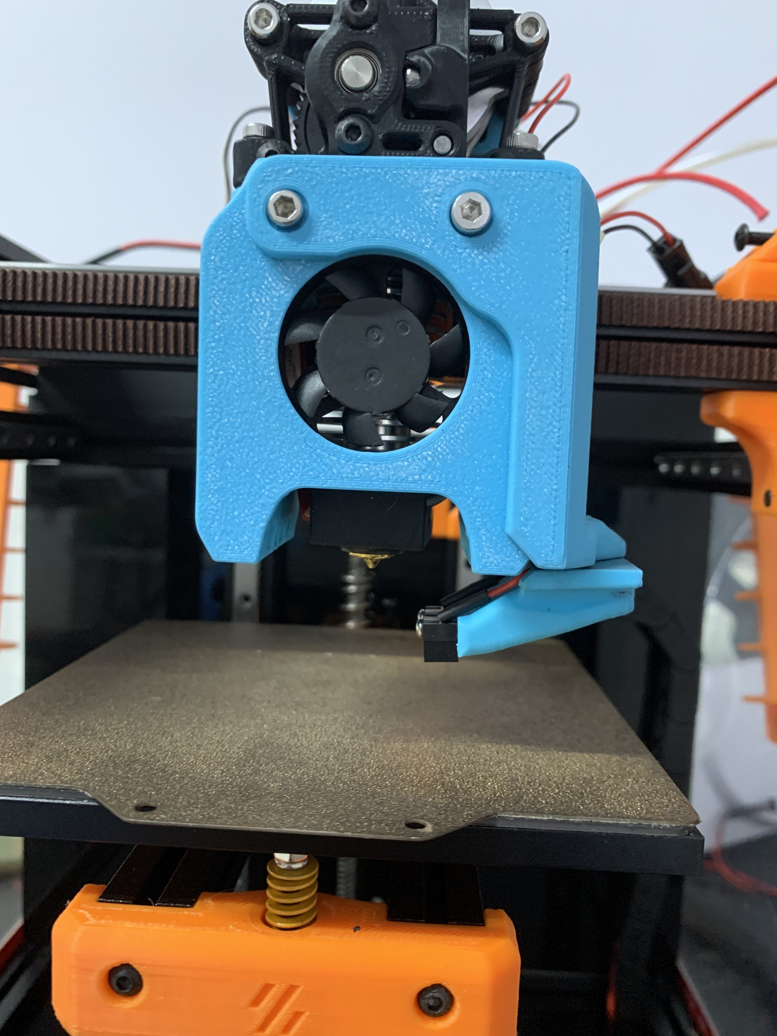
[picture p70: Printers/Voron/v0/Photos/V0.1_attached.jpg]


Route the probe mount cables to near the end of the V0 umbilical, install a male terminal in there.

**Before going further, please turn off the printer, the SKR boards are very picky with short circuits.**

Connect a female terminal to the wires that will run in the umbilical from the toolhead to the controller.

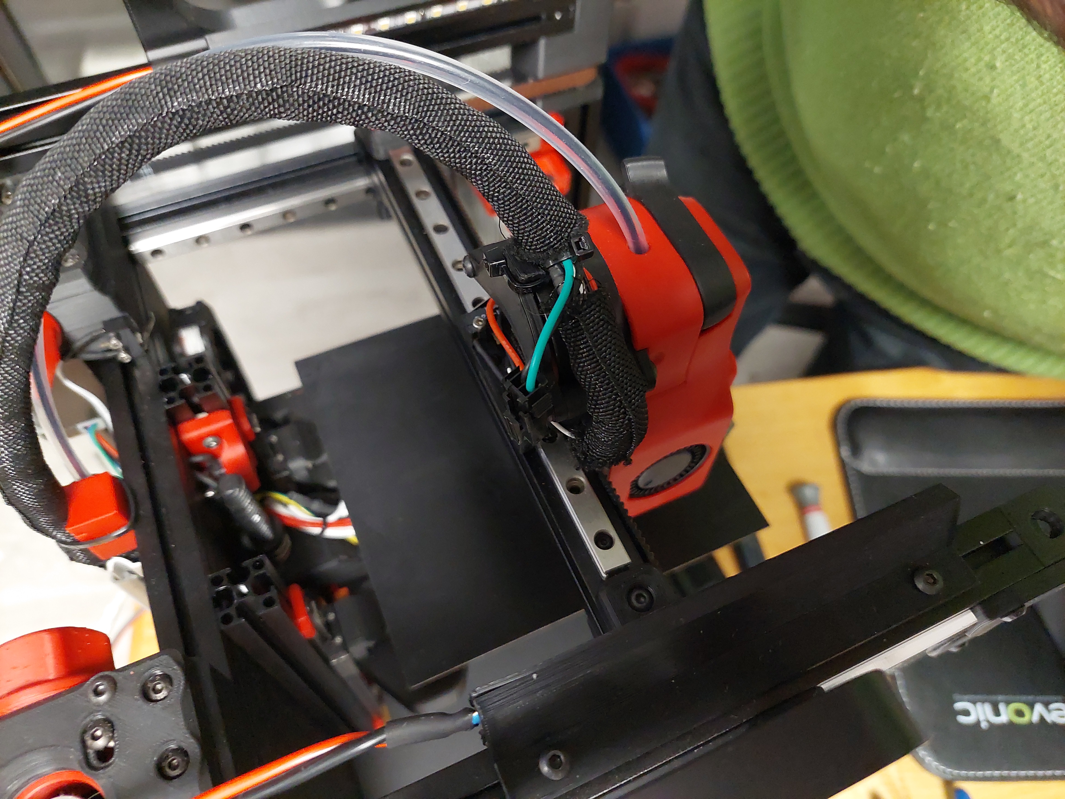
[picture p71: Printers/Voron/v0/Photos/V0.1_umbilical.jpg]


Connect the wires from the Klicky Probe to the Zprobe port, on GND and PC14 bin (I reused the LDO kit connector)

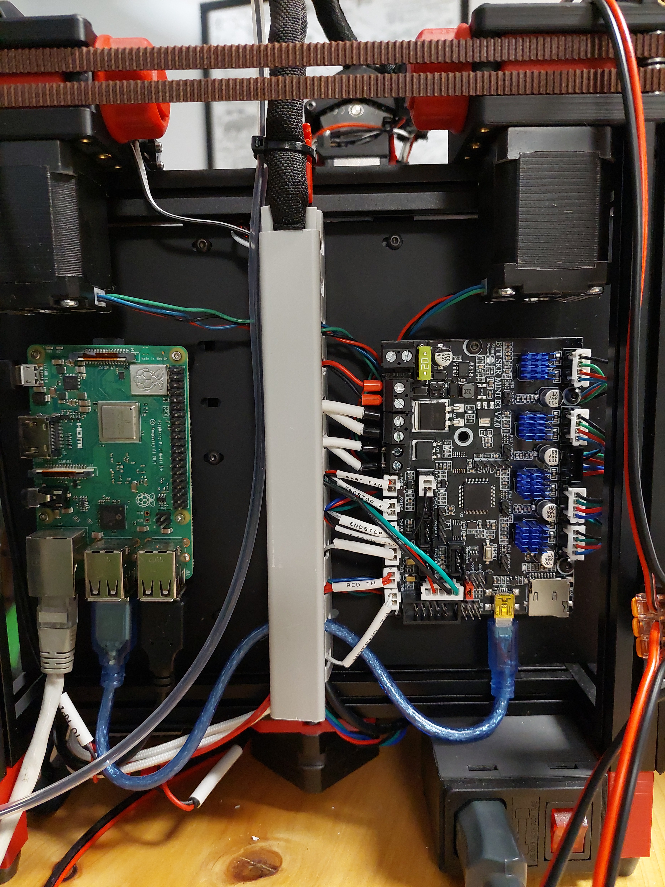
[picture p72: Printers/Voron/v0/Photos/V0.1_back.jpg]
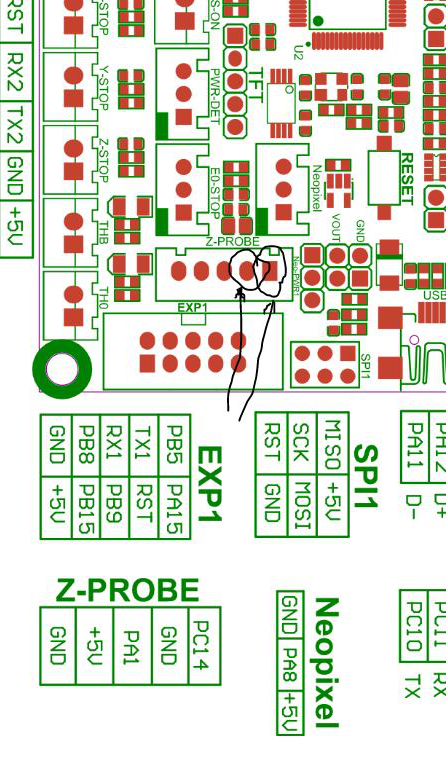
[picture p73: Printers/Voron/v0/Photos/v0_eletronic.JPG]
v0_eletronic
|  |  |
| --- | --- |

When testing the docking and attachment of the probe, make sure that the back magnet of the probe and the dock magnet do not touch, if they do, it will make attaching the probe much harder.

### Step 5: klipper configuration

Unfortunately, I do not know how to document RRF probe configuration, so here is only Klipper configurations.

As of right now, klipper and RRF have no inbuilt support for a removable probe, fortunately, it does support very robust macro programming, so you will need to add macros to be able to dock and attach the probe as necessary, as well as supporting the rest of the functions that require the usage of a probe.

The macros and instructions on how to configure are located on the [Macro directory](../../../Klipper_macros), you need to **check that before continuing on the build**, there are also some [RRF scripts](../../RRF_macros) that work for the Voron V2.4.

For the Voron v0, these are the recommended configuration on the klicky-variables.cfg:

```python
variable_verbose:               True  # Enable verbose output
variable_travel_speed:          100   # how fast all other travel moves will be performed when running these macros
variable_dock_speed:            50    # how fast should the toolhead move when docking the probe for the final movement
variable_release_speed:         55    # how fast should the toolhead move to release the hold of the magnets after docking
variable_z_drop_speed:          20    # how fast the z will lower when moving to the z location to clear the probe
    
variable_safe_z:         	    25    # Minimum Z for attach/dock and homing functions
# if true it will move the bed away from the nozzle when Z is not homed
variable_enable_z_hop:        True    # True v0
    
#Dock move
Variable_dockmove_x:             0    # Final toolhead movement to release
Variable_dockmove_y:            40    # the probe on the dock
Variable_dockmove_z:             0    # (can be negative)

#Attach move
Variable_attachmove_x:          30    # Final toolhead movement to Dock
Variable_attachmove_y:           0    # the probe on the dock
Variable_attachmove_z:           0    # (can be negative)
    
variable_max_bed_x:             120   # maximum Bed size avoids doing a probe_accuracy outside the bed
variable_max_bed_y:             120   # maximum Bed size avoids doing a probe_accuracy outside the bed

```

The sections below should be added to klicky-specific.cfg, that way, it will be loaded on klipper via a klicky-probe.cfg include.

If you would like to use a bed mesh, this is the recommended settings:

```python
[bed_mesh]
mesh_min: 15,15
mesh_max: 105,105
speed: 100
horizontal_move_z: 20 

probe_count: 3,3					#if you would like more detail, use 5,5 here
relative_reference_index: 4			 #if you use 5,5 above, place 12 here
move_check_distance: 3

algorithm: lagrange
fade_start: 1
fade_end: 10
fade_target: 0
split_delta_z: 0.0125
mesh_pps: 2,2
```

Regarding the Screws Tilt Adjust (Klipper probes the three screws positions and recommends the number of turns to level the bed), you can use this configuration as a reference, the probe should be over the screws when you do send the nozzle to the respective coordinate:

```python
[screws_tilt_adjust]
screw1: 100,115          #For Long probe
screw1_name: back right
screw2: 0,115            #For Long probe
screw2_name: back left
screw3: 60,5             #For Long probe
screw3_name: front screw
horizontal_move_z: 20
speed: 100
screw_thread: CW-M3
```

You should test this and adjust accordingly. 

This is probe configuration is with the default Voron v0.1 SKR mini E3 v2 configuration, with the probe connected to the PC14 pin, please update it to your specific configuration:

```python
[probe]
#with Long Klicky Probe
pin: ^PC14
x_offset: 8 #(9.5 with front cowling)
y_offset: 0
z_offset: 14.5
speed: 7
lift_speed: 7

samples: 3
samples_result: median
sample_retract_dist: 2

samples_tolerance: 0.01
samples_tolerance_retries: 10
```

I recommend a probing speed between 5mm/s and 10mm/s, you may experiment to see what is the better speed for your machine.
Please confirm that if you are not using a endstop pin, that the pull-up is enable by using the ^ sign, normally the endstop pins have a hardware solution that does not require this configuration.
Depending on your switch you may need to add a `!` to invert that pin (normally open vs. normally closed).

#### Z endstop and Probe configuration (virtual Z endstop)

If you want to use the Klicky Probe as your Z endstop, please read this [excellent documentation](https://github.com/T4KUUY4/Voron-Stuff/tree/main/KlickyProbeZoffset) by Takuya and Clee, as it was written for a Voron v2.4 you need to use the probe offsets that are defined in here.

#### Assembled Klicky Probe

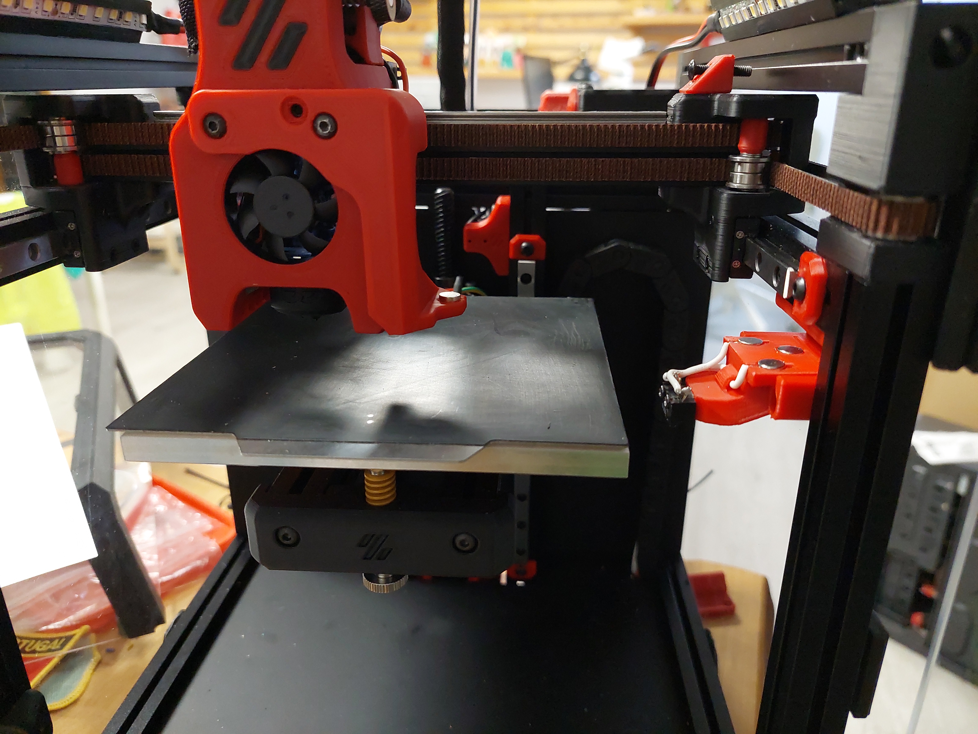
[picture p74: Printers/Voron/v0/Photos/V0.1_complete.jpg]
Assembled Klicky Probe


### Step 6: klipper  Dock/Undock  configuration
#### X max position adjustment

Even in the stock X endstop with a lever, you normally can add a extra mm of X travel due to the lever extra trigger distance:

```python
[stepper_x]
position_endstop: 120
position_max: 121
```

#### Adjust Probe Pickup Position

One of the last things we need to do is to adjust the probe pickup position.

Make sure that the x and y axis are homed and the probe is manually attached to mount.

Now manually (with gcode commands) move the toolhead to the probe dock and move it so far to the back that the probe docks, note the Y-Position.

Next, again manually, move the toolhead parallel to the probe dock until the probe it is perfectly aligned with the mount, note the X.Position.

Open your `klicky-variables.cfg` and find the `#dock location` section and edit the following two line

```python
variable_docklocation_x:
variable_docklocation_y:
```

Test now with the ATTACH_PROBE and DOCK_PROBE if it docks and is removed correctly, some common points that can give problems are:

* the dock magnet is touching the back probe magnet, they cannot touch, push them further in
* the probe is hitting the dock arms, please move the toolhead more to the side where the probe does not hit, by 1mm at a time, until it works
* the probe is falling after being release, the dock is too far away, you can insert one or several 1mm spacer to move the dock and solve this

***WARNING when you are doing PROBE_ACCURACY, make sure that the probe is above the bed, the PROBE_ACCURACY macro does not move the toolhead in X or Y.***

Congratulations, your done :).

## Firsts tests

Before starting to test klicky, and from past mistakes, please remove your PEI sheet (the probe works on the magnetic sheet) and if possible, change your printer maximum speed, acceleration and Z current, on klipper with TMC steppers, you can do this:

```python
SET_TMC_CURRENT STEPPER=stepper_z CURRENT=0.2 
SET_VELOCITY_LIMIT ACCEL=1000
SET_VELOCITY_LIMIT VELOCITY=50
```

Enjoy your Klicky Probe!

## Dock and undock video

https://youtu.be/qqRuQJcBS7o

It is working very well, if you decide to use it, give me feedback, either here, or on discord, my discord user is JosAr#0517.

By standing on the shoulders of giants, lets see if we can see further.

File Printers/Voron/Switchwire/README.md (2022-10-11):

# Klicky Probe for  Vorondesign Switchwire printers

Here you will find the necessary files and documentation to print and setup your own klicky probe on the Switchwire (finally).

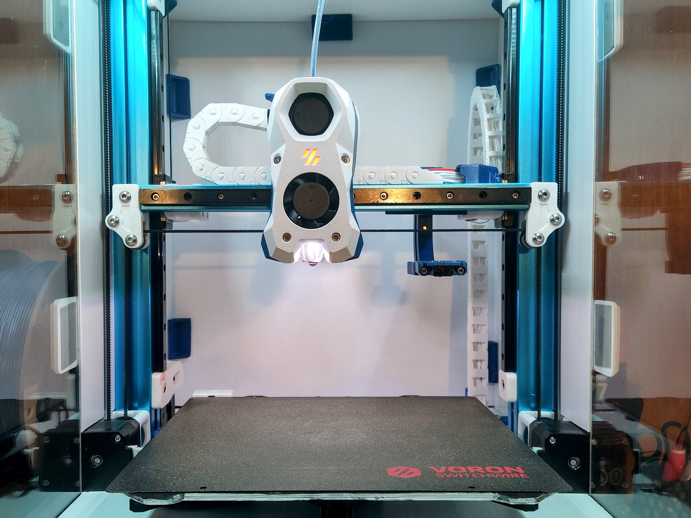
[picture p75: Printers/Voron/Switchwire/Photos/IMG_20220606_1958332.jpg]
Switchwire Klicky


It uses a slightly different approach than most magnetically attached probes, it's secured on the X extrusion, so it's available on any Z height and can be used without knowing the Z position, just like all the others.

I do not own a  Switchwire, so the tests were made with the help of the Voron community to whom i would like to thanks for the support, first and foremost to Patrice who was an excelent contributor to the project and main instigator, and also marciorssilva, Iconic FAB lv and Jason who tested and troubleshooted several components.

This directory has the STL files properly oriented for printing and community mods for the respective printer, there are [klipper](../../../Klipper_macros) macros and [RRF](../../../RRF_macros) macros on the repository.

You can find more information about the Voron printers at the [website](https://vorondesign.com/) or go check the [discord](https://discord.gg/voron), for the record, i own a v2.4, this is how i would describe them "A Voron is a fast high quality printer, i print with much better quality  the perimeters at the draft speed of my old bedslinger. It also has a  big community with lots of documentation and new ideas."

It has a servo powered dock on the X axis, the bed can be fully used during printing, and it can also be used without extra configurations as a virtual Z endstop.

Above all, have fun and be excellent to one another, now to the instructions.

This mod is not yet on [VoronUsers repository](https://github.com/VoronDesign/VoronUsers/tree/master/printer_mods/JosAr/Klicky-Probe), should be soon. 

They say an image is worth a 1000 words, but this is better described by a [small movie](https://youtu.be/if7qnrqHi_w), this was filmed by Patrice.

Some picture before heading to bussiness.

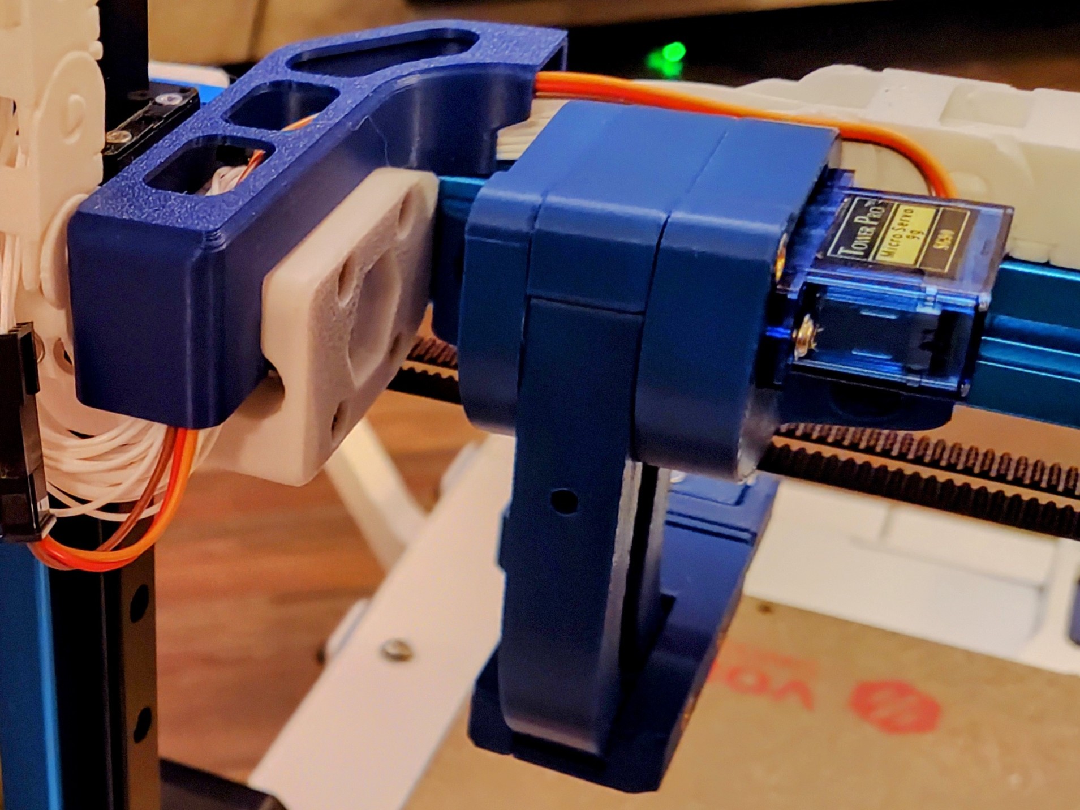
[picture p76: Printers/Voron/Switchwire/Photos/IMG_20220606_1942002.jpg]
backview
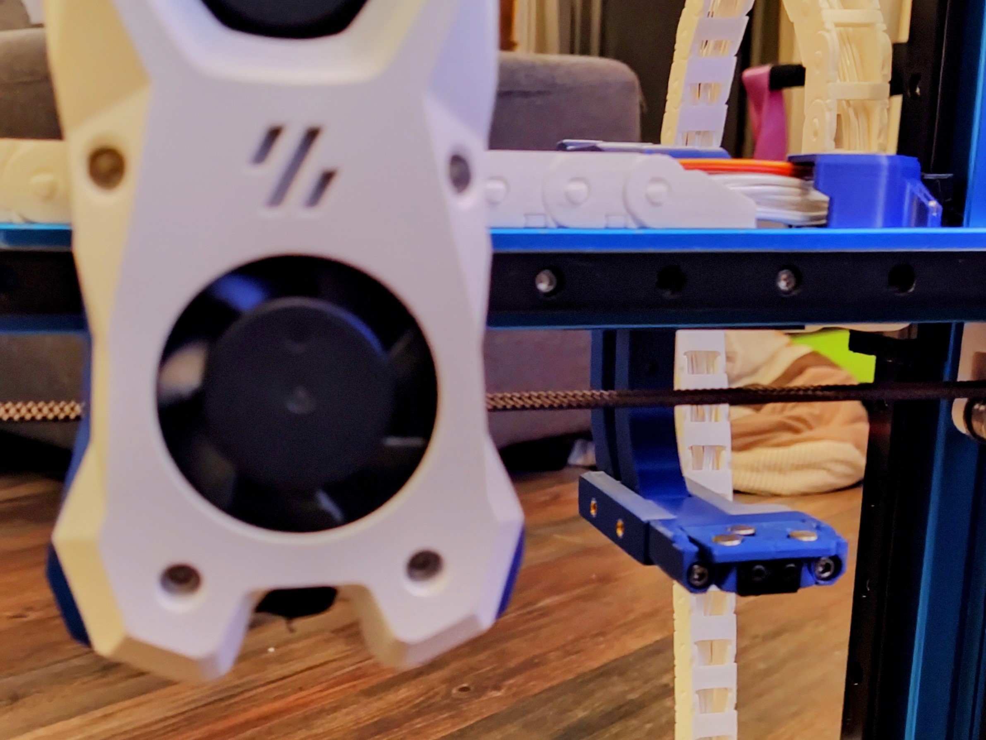
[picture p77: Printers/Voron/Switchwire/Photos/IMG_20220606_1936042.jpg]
sw_frontview
|  |  |
| --- | --- |

## Probe selection

Right now, there are two probe attachment options, each with two probe types.

### [Regular Klicky](../../../Probes/KlickyProbe/)

First klicky probe, based on the [Quickdraw probe](https://github.com/Annex-Engineering/Quickdraw_Probe), with an added third magnet for added stability and fixed dock gantry setups.

klickyprobe

It uses magnets to secure the probe to the mount and also to make the electrical connection.
The magnets can be glued to prevent them from coming loose.
It supports a microswitch probe and Unklicky ([invented by DustinSpeed](https://github.com/majarspeed/Unklicky)) (self built probe, that so far surpasses the microswitches in common use) based probing.

To assemble this probe, choose one and head to the assembly instruction below, the probe BOM is also there:

- [KlickyProbe](../../../Probes/KlickyProbe/)
- [Unklicky original (coiled wire variant, uses one 3x2 magnet)](https://github.com/majarspeed/Unklicky/tree/main/Unklicky)
- [Unklicky BFP-HS (heat set version, uses only 6x3 magnets)](https://github.com/majarspeed/Unklicky/tree/main/BFP-HS), should be more resilient over time
- [Unklicky BFP (coiled wire variant, uses only 6x3 magnets)](../../../Probes/Unklicky/)

### [KlickyNG](../../../Probes/KlickyNG/)

New enclosed magnets probe, it does not require glue to help prevent the magnets from coming loose, magnets are also self aligning.
This approach only uses common and easy to source parts.

klickyNGprobe

Also supports a microswitch probe and Unklicky ([invented by DustinSpeed](https://github.com/majarspeed/Unklicky)) (self built probe, that so far surpasses the microswitches in common use) based probing.

To assemble this probe, choose one and head to the assembly instruction below, the probe BOM is also there:

- [KlickyNG Probe](../../../Probes/KlickyNG/)
- [UnklickyNG original (coiled wire variant, uses two 3x2 (or 3x4) magnets)](../../../Probes/UnklickyNG/)
- [UnklickyNG BFP (coiled wire variant, uses only 6x3 magnets)](../../../Probes/UnklickyNG/)

## Bill of Materials (BOM)

### Tools:

- Multimeter to check for Continuity 
- Super Glue (optional)
- Soldering Iron to install the heat inserts

### Probe:

- check the links on the probe section above

### AB/SB mount:

- check the links on the probe section above

### Probe dock:

- check the links on the probe section above

### Servo mount

- 2x M3x24 mm SHC Screws
- 3x 1m 24AWG cable to connect the servo 
- 2x  threaded insert M3x5 mmx4 mm
- 2x M5x10 BHCS
- 2x M5 T-Nut for 2020 extrusion
- 1x MG90s servo with arms and mounting screws included

### Arms

- 4x 6 mm x 3 mm magnets (N35 recommended)
- 3x20 mm PTFE Tube (4mm OD 2mm ID) 
- 1x12 mm PTFE Tube (4mm OD 2mm ID) 

### Dock mount:

- 2x M3x20 mm SHC Screws
- 4x  threaded insert M3x5 mmx4 mm

## Sourcing

To get the best experience, please consider purchasing from the trusted list of suppliers bellow.

[trusted suppliers list](../../../Sourcing.md)

## Parts location

The probe STL's are located on each probe directory on the STL

The printer specific STL's are located [here](./SW_STL).

The CAD with all the parts are [here](../../../CAD).

## What to print

### Probe

follow the instructions on the Probe selection section

### AB/SB mount

follow the instructions on the Probe selection section

### Probe dock

follow the instructions on the Probe selection section

### Servo mount

- Servo_Mount_Body_right
- Servo_Mount_Body_center
- Servo_Mount_Body_left

### Arms 

- Drive_arm_front
- Drive_arm_back

### Dock mount

- Servo_dock_mount_right
- Servo_dock_mount_left
- 2x 2mm_extender (might be required)

### Printing instructions

Recommended printing settings:

* initial layer height:0,24
* layer height: 0.2mm
* bottom/top/perimeters: 4
* infill: more than 23%
* infill type: Cubic
* Thin walls: On

The recommended printing orientation is (the STL's are correctly oriented for printing):

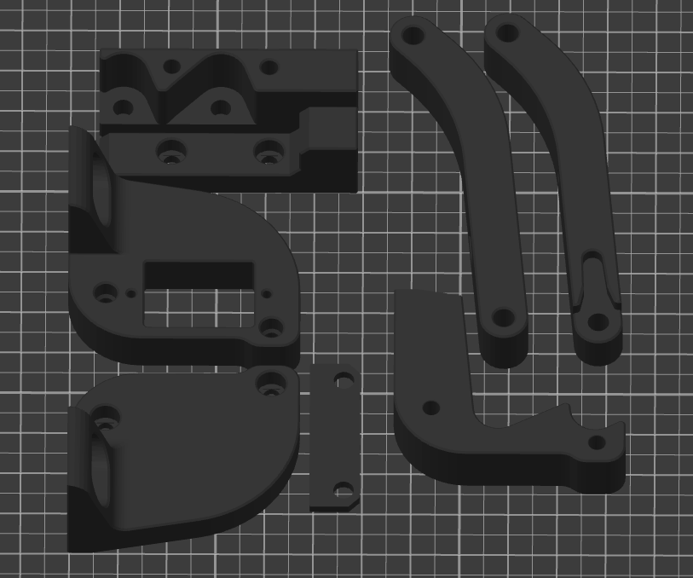
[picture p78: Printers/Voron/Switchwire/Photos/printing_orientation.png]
printing orientation


It was tested and printed with ABS, might work on other materials, if you try, let me know how it worked out.

### Components

Klicky Switchwire parts

## Assembly

### Step 1 - Servo arm preparation

Find the servo arm that fits the dock arm the best and cut off anything else on that arm if there is anything, tipically is the one that is circled.

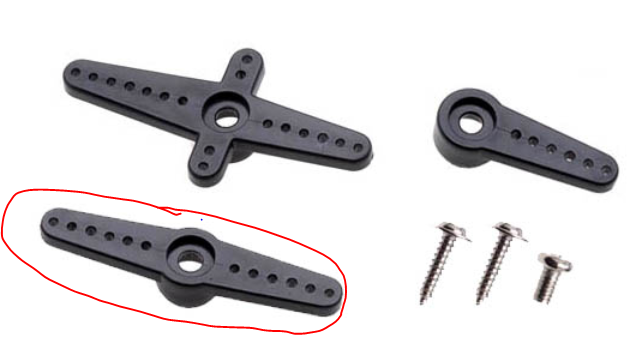
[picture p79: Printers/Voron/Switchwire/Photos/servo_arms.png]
servo_arms


servo_arms_cut

### Step 2 - Arms preparation

Insert 2 6x3 magnets on each arm socket.

Switchwire arms

Also insert the 3 20mm PTFE tubes and the 12 mm one on the arms as displayed on the picture:

Switchwire arms

### Step 3 - Dock mount

With the soldering iron tip, heat set the 4 threaded inserts like you did within your Voron build on the dock mount body, two on the top of each body and two on the side of the Servo_dock_mount_left:

| dock_mount1.1 | dock_mount1.2 |
| ---: | :--- |

Now attach the arms with the 20mm PTFE tube on the Servo_dock_mount_left part, take care to match the arms positions as they are on the image:

dock_mount2

Complete assembly by attaching the Servo_dock_mount_right and secure with 2x20 mm m3 screws  :

dock_mount3

### Step 4 - Servo mount

With the soldering iron tip, heat set the 2 threaded inserts like you did within your Voron build on the Servo_mount_body_left.

dock_mount2

Now attach the arms with the 20mm PTFE tube on the Servo_mount_body_right part, take care to match the arms positions as they are on the image:

dock_mount2

Insert the Servo_Mount_Body_center following the body contour:

dock_mount3

And complete assembly by attaching the Servo_Mount_Body_left and secure with 2x24 mm m3 screws:

dock_mount3

### Step 5 - Probe Dock assembly

Now attach the probe dock assembly that you want to use to the Dock arm with 2x16mm m3 screws.

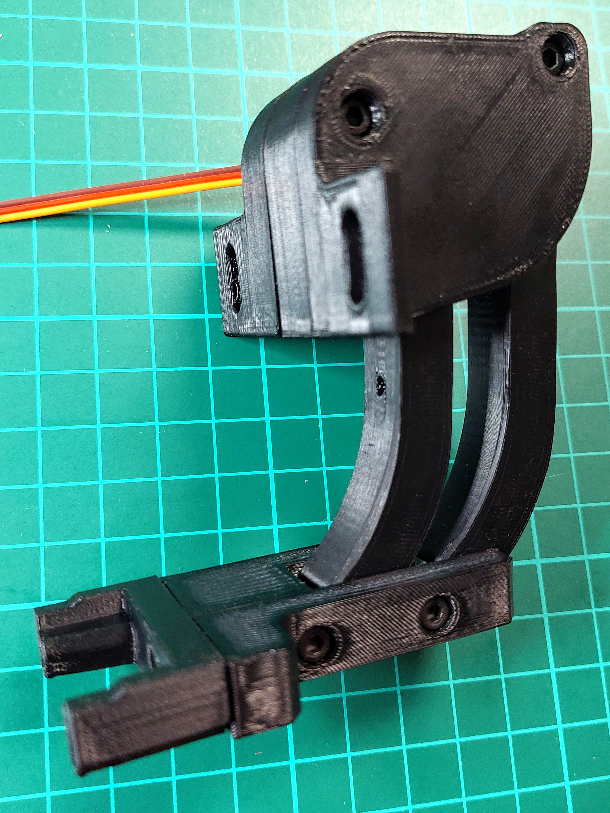
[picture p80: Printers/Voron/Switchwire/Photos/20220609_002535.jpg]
dock_mount4


Note: you may need to use later a dock extender to allow for easier probe docking and attaching.

### Step 6: Servo MCU configuration

To calibrate the servo, we will need to wire it temporarily to the MCU, you should use the same pins and configuration for the final setup, but for now the wires don't need to be very long, just long enough that you can work comfortably. 

The servo has 3 wires, as you can see from this picture:

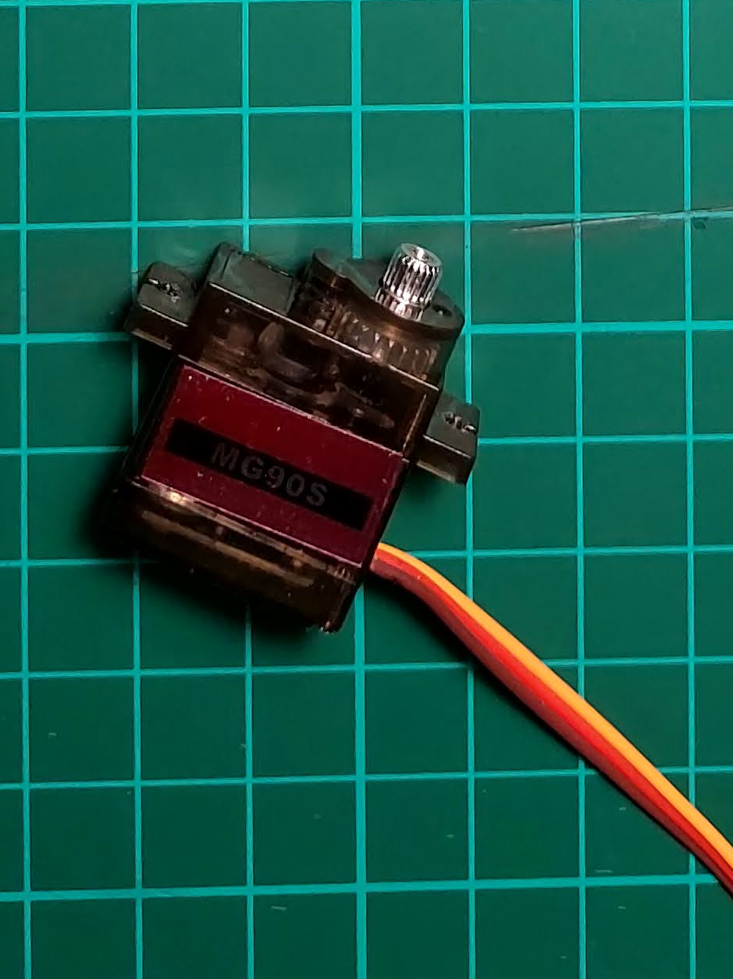
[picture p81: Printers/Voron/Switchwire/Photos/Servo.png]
servo


Normally, the GND is the brown, the red is the +5v and the orange is the PWM pin.

Servo diagram

The GND and PWM you wire to the MCU, on a SKR mini E3, you can use the PWR-DET or E0-STOP pins.

pins

The 5v, should be wired to the 5V PSU or to the same power supply of your raspberry pi, as the servo can use more power than the MCU 5v can supply.

The following klipper servo configuration should be added now to your printer.cfg, we will need it to calibrate the arms position. 

```python
[servo klicky_servo]
#check were your servo is wired
pin: PC12
maximum_servo_angle: 180
minimum_pulse_width: 0.00025
maximum_pulse_width: 0.0024

[gcode_macro _servo_test_angle]
gcode:
	{% set ANGLE  = params.ANGLE|int %}
	
    SET_SERVO SERVO=klicky_servo ANGLE={ANGLE}
    G4 P250
    SET_SERVO SERVO=klicky_servo WIDTH=0.0
```

restart klipper now, wire the servo and check if you can move it by issuing the following commands:

```python
_servo_test_angle angle=40
_servo_test_angle angle=130
```

Your servo should move more or less 90 degree between those two commands.

### Step 7: Servo calibration

The servo position needs to be reset, so that we can setup the angle easily.
Begin by issuing the instruction "_servo_test_angle angle=45" so that the servo will move to it's calibrated 45 degree position, then:

move the arms to the deploy position, like on the picture

servo

then attach the servo arm to it's place

servo

insert the servo on it's final place, attaching the arm to the servo pinion

servo

then remove the servo taking take that the arm is still attached to the pinion

servo

secure the arm with the included screw:

servo

and finally install the servo in its place and secure with the two included screws:

servo_installed

Test now with "_servo_test_angle angle=40" the arm should move fully to the deploy position, if it does not, you need to recheck the servo arm position, or decrease the angle, you can go until -90, remember that value.

Now, using the same macro, test the correct value for the arms to fully retract, start with the value above and add 10 or 5 degrees each time, preferably until the arms are touching one another.

Remember these values, you will need them later on klicky-variables configuration:

```python
variable_servo_deploy:          angle value with the arms on the deploy position
variable_servo_retract:         angle value with the arms on the retract position
```

### Step 8: Physical installation

- 2x M5x10 BHCS
- 2x M5 T-Nut for 2020 extrusion

The servo mount is mounted on the back of the X extrusion with two M5 T-Nuts, it has a M5 hole on each side of the servo mount that you secure to the extrusion.

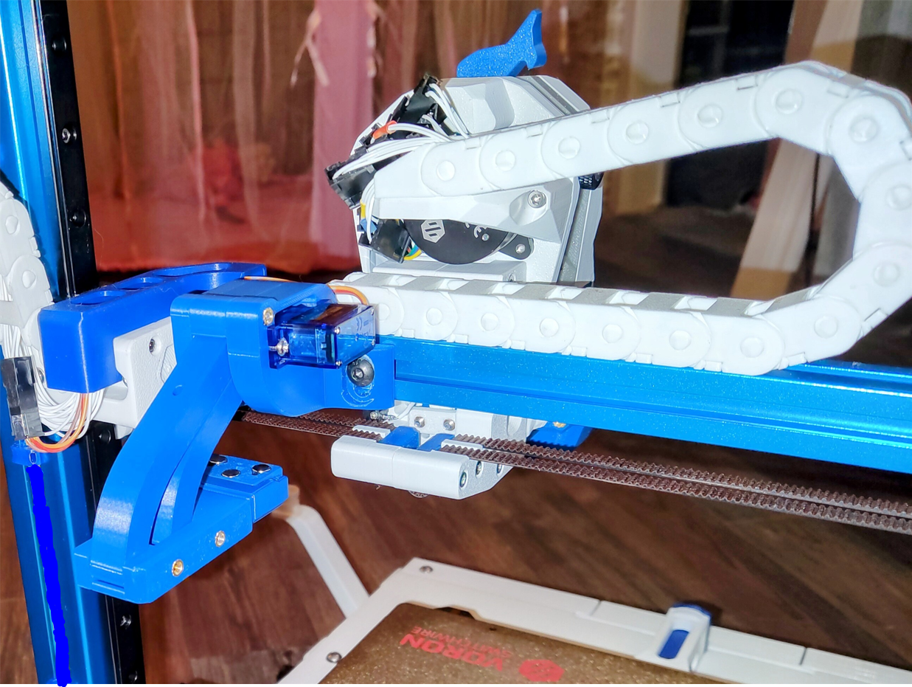
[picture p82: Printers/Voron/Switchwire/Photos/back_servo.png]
back_servo


Is is better to mount it near the Z cable chain so that the servo cable path is smaller and you can keep the stock servo cable, and just change the dupont end to a microfit or similar.

The servo mount is slightly adjustable on the Z, so you push the dock (with a probe) to the deploy position and attach the probe to the toolhead and then secure the servo dock in a position that can deliver the probe consistently to the toolhead mount.

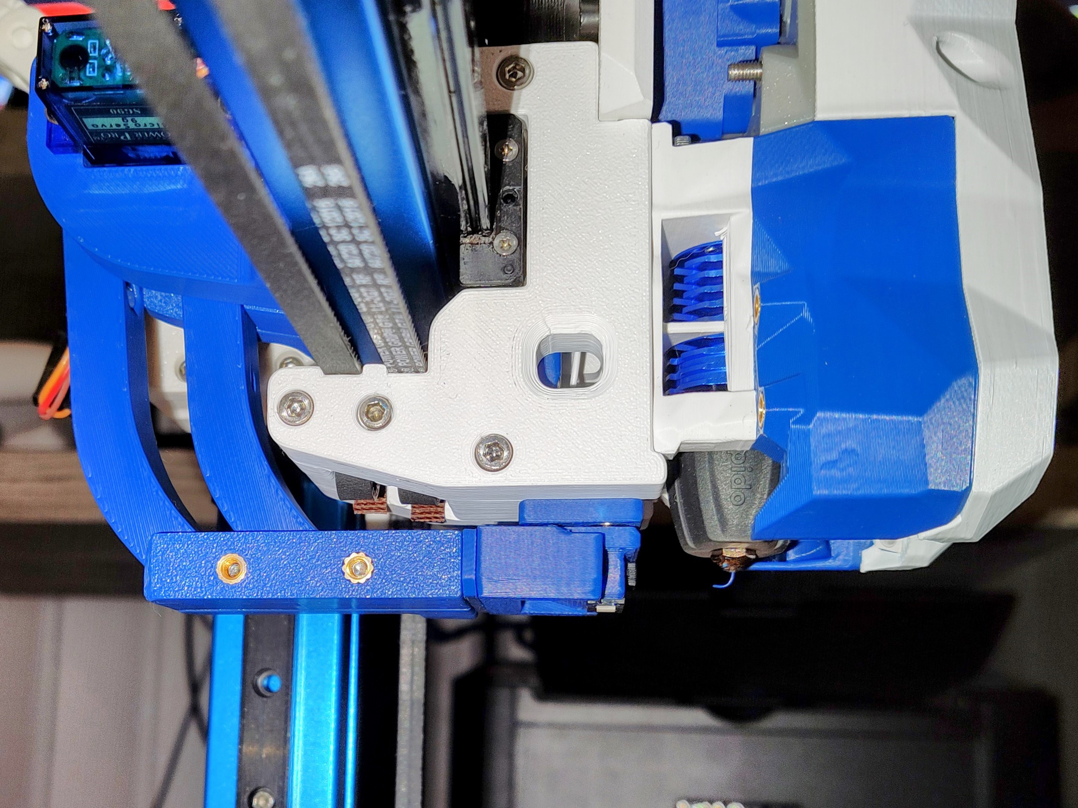
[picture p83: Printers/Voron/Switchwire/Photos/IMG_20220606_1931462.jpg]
servo_deployed


It should look like the image above when installed.

### Step 9: Servo Wiring on the chains

To wire the servo, it's recommended to use 3 new wires on the Z cable chain connected to a microfit or a JST female, that will connect to the servo cable like on the images bellow.

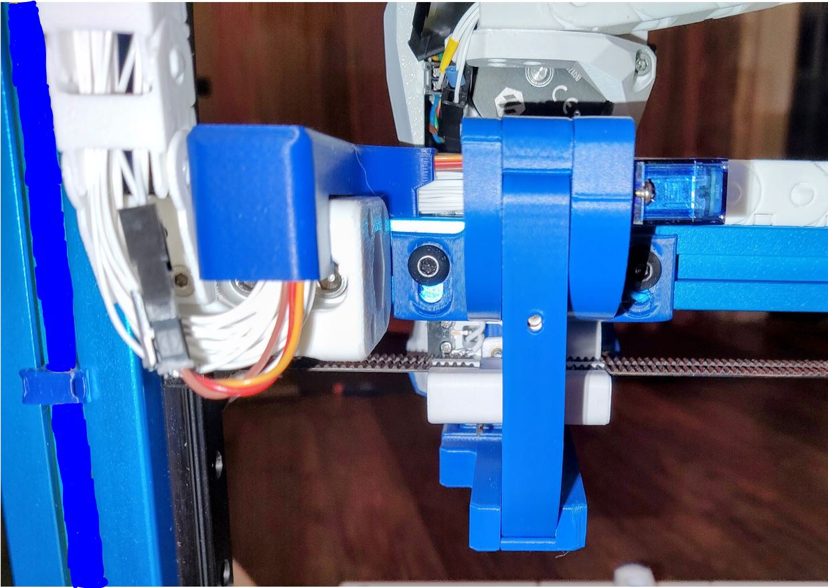
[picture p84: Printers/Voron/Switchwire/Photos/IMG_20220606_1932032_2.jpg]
wire_chains


Then connect and recheck the MCU connections and 5v PSU servo connections as you configured on step 6.

### Step 10: klipper configuration

Unfortunately, I do not know how to document RRF probe configuration, so here is only Klipper configurations.

As of right now, klipper and RRF have no inbuilt support for a removable probe, fortunately, it does support very robust macro programming, so you will need to add macros to be able to dock and attach the probe as necessary, as well as supporting the rest of the functions that require the usage of a probe.

The macros and instructions on how to configure are located on the [Macro directory](../../../Klipper_macros), you need to **check that before continuing on the build**, there are also some [RRF scripts](../../RRF_macros) that work for the Voron V2.4 and might work for the switchwire also.

For the Voron Switchwire, these are the recommended configuration on the klicky-variables.cfg:

```python
[gcode_macro _User_Variables]
variable_verbose:             True    # Enable verbose output
variable_debug:              False    # Enable Debug output
variable_travel_speed:         200    # how fast all other travel moves will be performed when running these macros
variable_move_accel:          1000    # how fast should the toolhead accelerate when moving
variable_dock_speed:            50    # how fast should the toolhead move when docking the probe for the final movement
variable_release_speed:         75    # how fast should the toolhead move to release the hold of the magnets after docking
variable_z_drop_speed:          20    # how fast the z will lower when moving to the z location to clear the probe

variable_safe_z:         	    25    # Minimum Z for attach/dock and homing functions
# if true it will move the bed away from the nozzle when Z is not homed
variable_enable_z_hop:        True    # set this to false for beds that fall significantly under gravity (almost to Z max)

variable_max_bed_y:            250    # maximum Bed size avoids doing a probe_accuracy outside the bed
variable_max_bed_x:            250    # maximum Bed size avoids doing a probe_accuracy outside the bed

# if a separate Z endstop switch is in
# use, specify the coordinates of the switch here (Voron).
# Set to 0 to have the probe move to center of bed
variable_z_endstop_x:            0
variable_z_endstop_y:            0

#Check the printer specific documentation on klipper Dock/Undock configuration, these are dummy values
#dock location 
variable_docklocation_x:      1000    # X Dock position
variable_docklocation_y:      1000    # Y Dock position
variable_docklocation_z:      -128    # Z dock position (-128 for a gantry/frame mount)

#The following variables are used if the dock is deployed and retracted via a servo motor
variable_enable_dock_servo:   True    # Set to true if your klicky dock is servo-controlled
variable_servo_name: 'klicky_servo'   # The name of the dock servo defined in printer.cfg under [servo]
variable_servo_deploy:          10    # angle value with the arms on the deploy position (found in step 7)
variable_servo_retract:         11    # angle value with the arms on the retract position (found in step 7)
variable_servo_delay:          250    # This is a delay to wait the servo to reach the requested position, be carefull with high values

#Dock move, final toolhead movement to release the probe on the dock
#it's a relative move
Variable_dockmove_x:           -40
Variable_dockmove_y:             0
Variable_dockmove_z:             0

#Attach move. final toolhead movement to attach the probe on the mount
#it's a relative move
Variable_attachmove_x:           0
Variable_attachmove_y:           0
Variable_attachmove_z:           0

```

This is probe configuration is with the default Switchwire SKR mini E3 v2 configuration, with the probe connected to the PC14 pin, please update it to your specific configuration:

```python
[probe]
Pin: ^PC2
x_offset: 0.0
y_offset: 19.75
z_offset: 6.17
speed: 5
lift_speed: 7
samples: 3
samples_result: median
sample_retract_dist: 2
samples_tolerance: 0.01
samples_tolerance_retries: 10
```

I recommend a probing speed between 3mm/s and 10mm/s, you may experiment to see what is the better speed for your machine.
Please confirm that if you are not using a endstop pin, that the pull-up is enable by using the ^ sign, normally the endstop pins have a hardware solution that does not require this configuration.
Depending on your switch you may need to add a `!` to invert that pin (normally open vs. normally closed).

**Remember that Switchwire uses the probe as the endstop, so you need to run probe_calibrate before printing**

### Step 11: klipper  Dock/Undock  configuration
#### Adjust Probe Pickup Position

One of the last things we need to do is to adjust the probe pickup position.

Home the X axis of your printer, then manually (with G0 X or GUI moves) move the toolhead until you can simulate with sucess the docking and attaching of the probe to the toolhead mount, use this value.

Open your `klicky-variables.cfg` and find the `#dock location` section and edit the following two line

```python
variable_docklocation_x: #what you found above
variable_docklocation_y:125 #middle of the bed
```

Test now with the ATTACH_PROBE and DOCK_PROBE if it docks and is removed correctly, some common points that can give problems are:

* the dock magnet is touching the back probe magnet, they cannot touch, push them further in
* the probe is hitting the dock arms, please move the toolhead more to the side where the probe does not hit, by 1mm at a time, until it works
* the probe is falling after being release, the dock is too far away, you can insert one or several 1mm spacer to move the dock and solve this
* the probe is not attaching to the mount, the dock is too far away, you can insert one or several 1mm spacer to move the dock and solve this

***WARNING when you are doing PROBE_ACCURACY, make sure that the probe is above the bed, the PROBE_ACCURACY macro does not move the toolhead in X or Y.***

Congratulations, your done :).

## Firsts tests

Before starting to test klicky, and from past mistakes, please use either the metal side of your PEI or your most damaged sheet and if possible, change your printer maximum speed, acceleration and Z current, on klipper with TMC steppers, you can do this:

```python
SET_TMC_CURRENT STEPPER=stepper_z CURRENT=0.2 
SET_VELOCITY_LIMIT ACCEL=1000
SET_VELOCITY_LIMIT VELOCITY=50
```

Enjoy your Klicky Probe!

It is working very well, if you decide to use it, give me feedback, either here, or on discord, my discord user is JosAr#0517.

By standing on the shoulders of giants, lets see if we can see further.

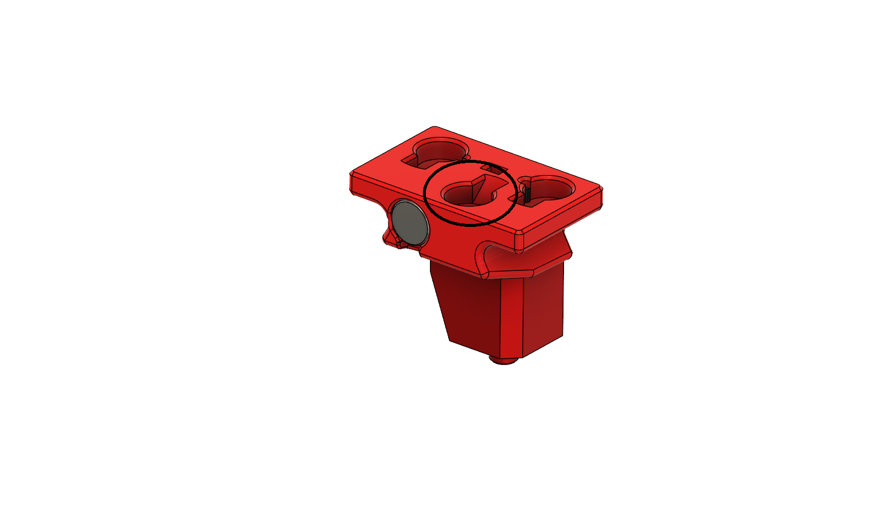
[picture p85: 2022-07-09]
Printers/Ratrig/VCore3.0_3.1/Photos/8.png

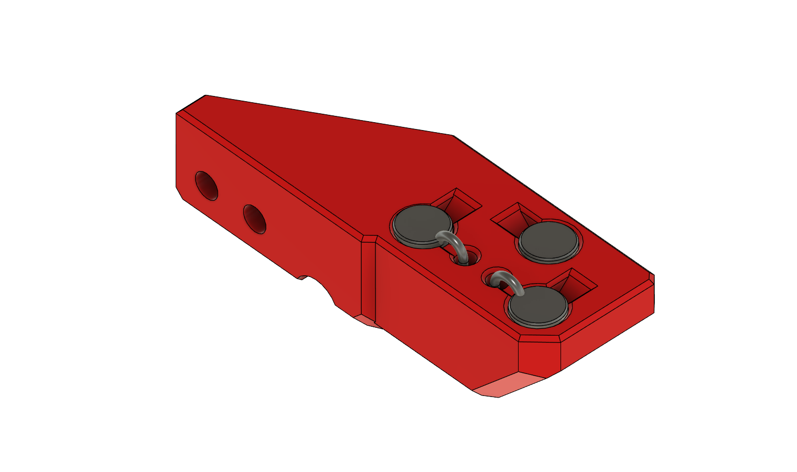
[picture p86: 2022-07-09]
Printers/Ratrig/VCore3.0_3.1/Photos/14.png

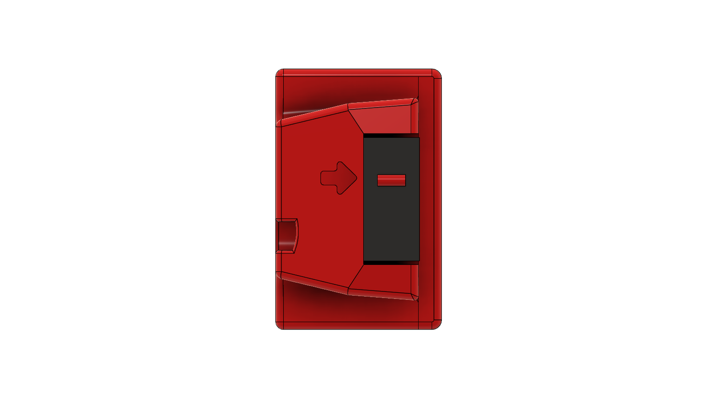
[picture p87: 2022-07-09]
Printers/Ratrig/VCore3.0_3.1/Photos/5.png

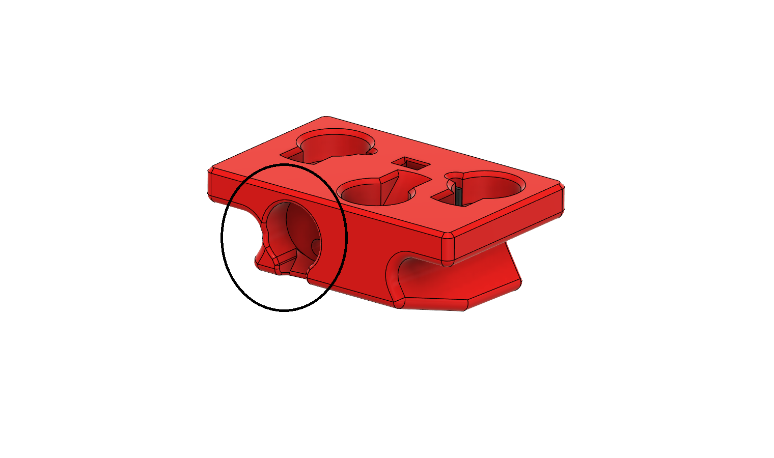
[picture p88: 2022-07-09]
Printers/Ratrig/VCore3.0_3.1/Photos/4.png

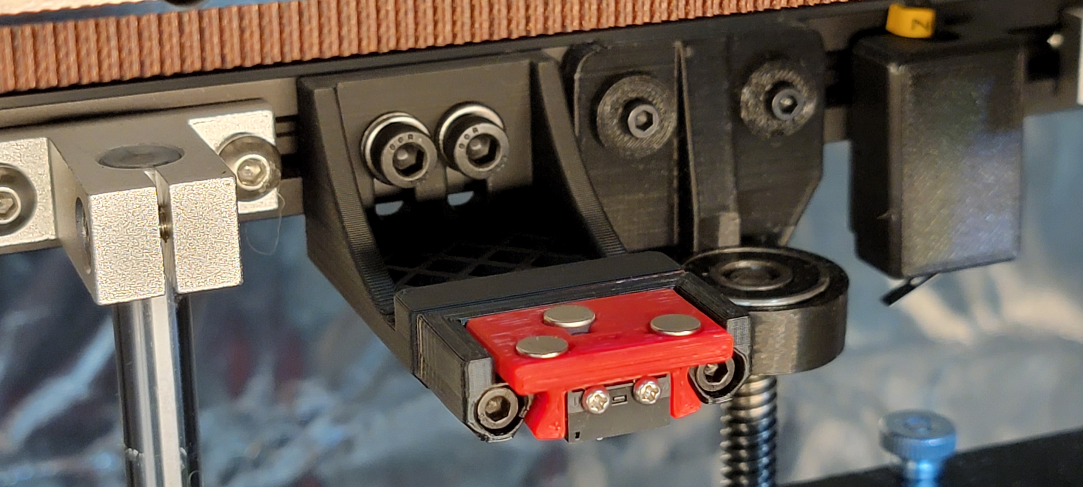
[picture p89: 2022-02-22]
Printers/ZeroG/Mercury_One/Photos/zerog-merc1-closeup.jpg

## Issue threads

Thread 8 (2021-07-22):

Probe_Calibrate Error

dsmith777, 2021-07-22:
Hello,

When running probe_calibrate with the Klicky probe, I get an error when I try to accept the results.

Error:
Manual probe failed! Use TESTZ commands to position the nozzle prior to running ACCEPT.

If I modify Probe_Calibrate in the klicky-probe.cfg, and comment out a few lines (Dock_Probe and Restore GCODE), I am able to manually remove the probe and finish the probe calibration with a successful accepting of the results.

Lines commented out:
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

This is my first time creating an issue on GitHub, so if you need anything further from me, just ask.

Thanks,

Dave

dsmith777, 2021-07-22:
After some discourse on the Voron Discord server, alexz V2.660 posted his workaround/fix for the issue.
https://github.com/zellneralex/klipper_config/blob/master/magprobe.cfg#L202
I will modify/add his macros that deal with this issue to the klick-probe.cfg, and get back to you guys.

dsmith777, 2021-08-04:
I tried adding those macro's from Alexz, but it didn't work for me.

jlas1, 2021-08-04:
Hi, so commenting these two lines did not solve the issue?

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

dsmith777, 2021-08-05:
Commenting those lines out fixed the issue, but I had to remove the probe manually to finish the probe_calibrate.

dukeduck1984, 2021-08-10:
Hi, I have the same issue.  Is there a fix rather than the manual workaround mentioned by @dsmith777 ?

QnzLAMBONE, 2021-08-16:
This should work. Relocated the save_gcode_state to after the probe_calibrate is performed

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

jlas1, 2021-08-16:
Will try this, thanks

dsmith777, 2021-08-17:
QnzLAMBONE's change, worked for me.

QnzLAMBONE, 2021-08-17:
It should actually look like this so that you restore the location from before attaching the probe, and then you restore the location of where the bed is probed.

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

Xperie, 2021-08-20:
I tried all the suggested solutions and I still get "Manual probe failed! Use TESTZ commands to position the nozzle prior to running ACCEPT." Can I manually add the value it gives me to printer.cfg?

QnzLAMBONE, 2021-08-20:
What you may have to do is manually tell your toolhead to move to the center of your bed, like your homing override would do. What happens is if you perform a G28 and then try to probe_calibrate, during the G28 it automatically docks the probe as part of the homing sequence. So probe_calibrate sees the docking location as the original location prior to running the command. So something like "G1 X125 Y125 Z5" before "probe_calibrate" will allow you to probe the center of the bed. And with the changes mentioned above the calibration should work after that

QnzLAMBONE, 2021-08-20:
What could also be done is you change the attach_probe macro so that it sends the toolhead to the center of the bed. And you can then comment out the first save_gcode_state and restore_gcode_state lines.

Xperie, 2021-08-20:
I tried with both the original Macro with the two lines commented out and with your updated one. Home my toolhead, then I run ATTACH_PROBE and then do G1 X175 Y175 Z10. I then run the PROBE_CALIBRATE command and it does its thing. After which it asks me to input ACCEPT or ABORT. I've tried both leaving the probe on and inputting ACCEPT and taking the probe off and inputting ACCEPT both give me the error. But with your updated code it gives about a 30 second pause before giving me the  "Manual probe failed! Use TESTZ commands to position the nozzle prior to running ACCEPT." error if I leave the probe on. Every other time it immediately gives me an error.

QnzLAMBONE, 2021-08-20:
Can you post your config for klicky_probe.cfg, I could take a look and see if I spot anything

Xperie, 2021-08-20:
`# This macro was provided by discord user Garrettwp to whom i give my thanks for sharing it with me.
# I have tweaked it a lot.
#
# this macro is  based on the great Annex magprobe dockable probe macros "#Originally developed by Mental, modified for better use on K-series printers by RyanG and Trails"
# that macro can be found here https://github.com/Annex-Engineering/Annex-Engineering_Other_Printer_Mods/blob/master/All_Printers/Microswitch_Probe/Klipper_Macros/dockable_probe_macros.cfg
#
# by standing on the shoulders of giants, lets see if we can see further

[probe]
pin: PG11 # input pin for the mag-probe
x_offset: 0
y_offset: 19.75
z_offset: 6.42
speed: 4.0
lift_speed: 8.0
samples: 5
samples_result: median
sample_retract_dist: 1.5
samples_tolerance: 0.01 #0.007
samples_tolerance_retries: 10

[gcode_macro User_Variables]
variable_verbose:               True  # Enable verbose output
variable_travel_speed:          200   # how fast all other travel moves will be performed when running these macros
variable_dock_speed:            50    # how fast should the toolhead move when docking the probe for the final movement
variable_release_speed:         100    # how fast should the toolhead move to release the hold of the magnets after docking
variable_z_drop_speed:          20    # how fast the z will lower when moving to the z location to clear the probe
variable_home_z_height:         15    # Z when homing

# if a separate Z endstop switch is in
# use, specify the coordinates of the switch here (Voron).
# Set to 0 to have the probe move to center of bed
variable_z_endstop_x:           232
variable_z_endstop_y:           347
#variable_z_endstop_x:          0
#variable_z_endstop_y:          0

# location to park the toolhead
variable_park_toolhead:         False  # Enable toolhead parking
variable_parkposition_x:        175
variable_parkposition_y:        175
variable_parkposition_z:        30

#dock location
variable_docklocation_x:        45    # X Dock position
variable_docklocation_y:        350   # Y Dock position
variable_docklocation_z:        15    # Z dock position
variable_dockarmslenght:        30    # Dock arms lenght, toolhead movement necessary to clear the dock arms

#Umbilical to help untangle the umbilical in difficult situations
variable_umbilical_x:           15    #X umbilical position
variable_umbilical_y:           15    #Y umbilical position
variable_umbilical:             False #should we untabgle the umbilical

# Do not modify below
gcode:
    {% set Mx = printer['configfile'].config["stepper_x"]["position_max"]|float %}
    {% set My = printer['configfile'].config["stepper_y"]["position_max"]|float %}
    {% set Ox = printer['configfile'].config["probe"]["x_offset"]|float %}
    {% set Oy = printer['configfile'].config["probe"]["y_offset"]|float %}
    {% set Oz = printer['configfile'].config["probe"]["z_offset"]|float %}

    # if docklocation_z is zero, use Home Z height for safety
    {% if docklocation_z == 0 %}
        SET_GCODE_VARIABLE MACRO=Probe_Variables VARIABLE=docklocation_z VALUE={ home_z_height }
    {% endif %}

    # If x, y coordinates are set for z endstop, assign them
    {% if z_endstop_x != 0 or z_endstop_y != 0 %}
        SET_GCODE_VARIABLE MACRO=Probe_Variables VARIABLE=z_endstop_x VALUE={ z_endstop_x }
        SET_GCODE_VARIABLE MACRO=Probe_Variables VARIABLE=z_endstop_y VALUE={ z_endstop_y }

    # if no x, y coordinates for z endstop, assume probe is endstop and move toolhead to center of bed
    {% else %}
        SET_GCODE_VARIABLE MACRO=Probe_Variables VARIABLE=z_endstop_x VALUE={ (Mx * 0.5) - Ox }
        SET_GCODE_VARIABLE MACRO=Probe_Variables VARIABLE=z_endstop_y VALUE={ (My * 0.5) - Oy }
    {% endif %}

[gcode_macro Probe_Variables]
variable_probe_attached:            False
variable_probe_state:               False
variable_probe_lock:                False
variable_z_endstop_x:               0
variable_z_endstop_y:               0
gcode:

[gcode_macro Homing_Variables]
default_parameter_reset:            0
gcode:
    {% set R  = params.RESET %}

    {% if R %}
        SET_GCODE_VARIABLE MACRO=Probe_Variables VARIABLE=probe_lock VALUE={ False }
   {% endif %}
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
QnzLAMBONE, 2021-08-21:
> https://pastebin.com/nBPHXTK0
>
> This is my klicky_probe.cfg. Thanks for trying to help.

In the config you sent you have the first RESTORE_GCODE_STATE commented out. The one right after Attach_Probe, without restoring the location after attaching the probe you'd end up probing at your dock instead

Xperie, 2021-08-21:
Ok I did the changes you said and I noticed something weird. The Toolhead drifts off to Y 194.75 after probing the bed. I have a feeling thats whats causing the issue but I have no idea why its doing it.

Xperie, 2021-08-21:
So what its doing when I PROBE_CALIBRATE now after homing is it grabs the probe > parks in the center at 175,175,15 > Begins probing > after probing it drifts over to Y 194.75 > saves that location > docks the probe > parks > then restores the 175,194.75,15 location.

Xperie, 2021-08-21:
Well I figured out the drifting its moving the toolhead to the probes offset afterwards. Is that supposed to happen?

Xperie, 2021-08-21:
I figured it out thanks for the help

QnzLAMBONE, 2021-08-21:
> Well I figured out the drifting its moving the toolhead to the probes offset afterwards. Is that supposed to happen?

Yes that is supposed to happen, thats how you set your offset after you probe the bed, it moves the nozzle to right above where you probed. Glad we got it figured out, what was wrong?

Xperie, 2021-08-21:
Not really sure, I reset my printer.cfg to default and then went through and set everything up again and it just worked.

jlas1, 2021-08-24:
I have pushed an updated PROBE_CALIBATE macro based of the feedback from this issue, it seems to work, it is working for me.
I'll close the issue, if necessary we will reopen it.

lrstanley, 2021-08-27:
I think there are a few issues caused by the recent changes in https://github.com/jlas1/Klicky-Probe/commit/0eb982421553e31b5fccbc38a7efbbcf2708da0f, and maybe this is also me being new to the macros, but...

PROBE_ACCURACY will error because the first gcode save starts with a prefix, but then it tries to restore without a prefix:

https://github.com/jlas1/Klicky-Probe/blob/670bf00428b20fde11c5511d73d1c58567a0776f/Klipper%20macro/klicky-probe.cfg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

Specifically `_original_nozzle_location` vs `original_nozzle_location`

Secondly, QGL, and similar commands work without issue for me, but with the macro that's currently in this repo, if I:

1. correct the above issues
2. probe X, Y, and Z (not using klicky as a z-endstop)
3. run PROBE_ACCURACY or PROBE_CALIBRATE

It will:

1. Drop or raise to necessary configured Z homing height
2. Attach probe
3. Move to Z-Endstop position
4. Lower as if it's going to use the z-endstop, but crash right into it

Again, QGL, and similar work without issues, so I suspect it's specifically with PROBE_ACCURACY and PROBE_CALIBRATE, I just commented out some of the save/restore gcodes, as follows:

```
    # Go to Z safe distance before saving location in order to
    # avoid crashing the probe on the bed when coming back
    G1 Z{Hzh} F{Sz}
    M400 # mandatory to save the new safe position
    SAVE_GCODE_STATE NAME=_original_nozzle_location

    CheckProbe action=query
    Attach_Probe

    #Restore nozzle location to probe the right place
    #RESTORE_GCODE_STATE NAME=_original_nozzle_location MOVE=1 MOVE_SPEED={St}

    _PROBE_ACCURACY {% for p in params
            %}{'%s=%s ' % (p, params[p])}{%
           endfor %}

    #store current nozzle location
    # SAVE_GCODE_STATE NAME=_original_nozzle_location

	Dock_Probe

    # Restore nozzle location again at the end
    RESTORE_GCODE_STATE NAME=_original_nozzle_location MOVE=1 MOVE_SPEED={St}
```

The above (which saves before attaching, and after docking) simply moved it right onto the bed and probed about 10mm away from the dock location, and ran the accuracy test like expected. It didn't try and do anything with the Z-Endstop.

I'm not sure if the above still solves whatever the original problems were, but it prevented the nozzle crash for me...

Closed 2021-08-24.

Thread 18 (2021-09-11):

Probe Attach Failed

deathfrombelow, 2021-09-11:
First time I homed z and it picked up the probe, undocked, but then stopped and gave me this: !! Error evaluating 'gcode_macro SetProbeState:gcode': CommandError: Probe attach failed!  But the probe is attached.

Is this possibly a signal issue?  Because when testing the probe signal (query_probe) I could not get it to work properly.  I have an octopus board and for prior induction probe, I split power to probe port (PB7) and signal to diag7 port (PG15) with diode.  Klicky did not work on PG15, so I switched it back to the probe port PB7, but it also did not work.  Both ports I used with and without the pull up (^) with no difference.  It was either always triggered or always open.

EDIT: It was signal issue.  I had continuity issues from the magnets not quite contacting each other, fixed by trimming wiring insulation where it bends.

jlas1, 2021-09-28:
Thanks for the feedback

Closed 2021-09-28.

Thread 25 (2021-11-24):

Found some issues with the macro caused by nesting macros

dancat, 2021-11-24:
Hi,

I have a corexy printer with moving bed (tiny-M) and I am using the macros from Klicky probe. I found a problem that during the homing override procedure, the bed is moved to the safe distance even if this is not needed. This is not good if the bed is at its lowest when the printer tries to move it.
While investigating this, I found the following in the klipper docs (https://www.klipper3d.org/Command_Templates.html): Important! Macros are first evaluated in entirety and only then are the resulting commands executed. If a macro issues a command that alters the state of the printer, the results of that state change will not be visible during the evaluation of the macro. This can also result in subtle behavior when a macro generates commands that call other macros, as the called macro is evaluated when it is invoked (which is after the entire evaluation of the calling macro).

The problem here is that when the AttachProbe macro is called on its own, the checks to move or not the bed work because checking if Z is homed will give the real answer. If the AttachProbe macro is called from anothe macro (like HomingOverrirde) the check if Z is homed will no longer give the real status, but will give it as if the calling macro was already executed (so it will always say Z is homed).

I guess this could be avoided by using some global variables instead of the home axis check in the macros themselves. I will have a go to this and see if I can make it work. But I thought to let you know in case this is something you were not aware of. This thing might affect all the checks done to the printer status from within macros if they are called nested, so probably the safest is to always check global variables in macros...

Best regards,
Daniel

jlas1, 2021-11-24:
Hi Dancat, can you check the latest macros, it should have that issue solved if the bed is configured in the gravity variable.
It will not move the bed anymore before homing.

jlas1, 2021-11-24:
with what probe are you using the klycky macros, just curious.

dancat, 2021-11-24:
Hi, thanks for feedback. I used an euclid probe. I'll have a look again at the last version and get back with feedback.

Best regards,
Daniel

Closed 2021-11-27.

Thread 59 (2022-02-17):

Magnets magnetizes the nozzle

bjoern79de, 2022-02-17:
I'm running Voron2.4/afterburner with Dragon-Hotend.
When the toolhead travels over the probe, the heatblock/nozzle gets magnetized, so that the nozzle pulls the endstop rod out.
I've solved it by keeping the retract low and adding an additional "horizontal retract" afterwards.

jlas1, 2022-02-17:
I think you will find that what is happening is that the endstop rod is being pulled by the AB mount magnets.
What I see pulling the endstop sometimes is a little bit of melted plastic on the tip, than when squashed functions for a while as a glue.

bjoern79de, 2022-02-18:
I can preclude melted plastic, because I removed the filament and used a new clean (and cold) nozzle.
When I travel directly to the endstop, the endstop rod isn't pulled by the AB mount magnets. But when the AB-mount travels over the probe (a few seconds ago) the endstop-rod keeps hanging under the nozzle tip.

jlas1, 2022-02-18:
can you send me an image of a movie, never heard of that before.

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

TravisWilder, 2022-02-18:
the nozzle should never touch an come close to the magnets - so this seem very strange

jlas1, 2022-03-02:
Could you post the images so that we can troubleshoot this further?

bjoern79de, 2022-03-03:
Sorry, I've replaced the hotend in the meanwhile and can't reproduce the issue anymore.
In the end I'm sure that the heatblock was magnetic and I don't know why exactly.
Maybe you can add the following hint to the README:

If that issue occurs, add the following gcode the _Home_Z-macro before lifting the nozzle:
`G91`
`G0 X10 F{z_drop_feedrate}`
`G90`

jlas1, 2022-03-04:
thanks for the feedback, i will keep that code in mind if this issue is more widespread.
Glad that it's working ok now.

Closed 2022-03-04.

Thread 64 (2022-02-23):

Bed mesh -Probe triggered prior to movement-

GN1G, 2022-02-23:
Hello,

my QGL works normal and without problems.
But if I run a Bed_Mesh_Calibration, it probes 3-4 points and then says "Probe triggered prior to movement"

Any ideas what can cause this?

best regards
GN1G

jlas1, 2022-02-23:
Most likely a cabling issue, check the crimps of your cable.
It can also be a broken wire on the chain, go to the location that you get the "Probe triggered prior to movement" on bed mesh and do a probe_accuracy to see if you manage to trigger it.

GN1G, 2022-02-23:
> Most likely a cabling issue, check the crimps of your cable. It can also be a broken wire on the chain, go to the location that you get the "Probe triggered prior to movement" on bed mesh and do a probe_accuracy to see if you manage to trigger it.

Thank you, I'll check it.

DorjeDorf, 2022-02-24:
What temps are you running the mesh at? I'd assume you have your bed piping hot as well as the nozzle?
I found that with crappier magnets, you need to drop the temp on the nozzle to 130-160C to have the magnets not be impacted by the temps and lose connectivity.

jlas1, 2022-02-24:
I never noticed that, the magnets above more or less 80 degrees they start to lose strenght, but that is very hard to happen, at least with a silicone sock on the heat block.

GN1G, 2022-02-25:
> What temps are you running the mesh at? I'd assume you have your bed piping hot as well as the nozzle? I found that with crappier magnets, you need to drop the temp on the nozzle to 130-160C to have the magnets not be impacted by the temps and lose connectivity.

The problem came from the stepper cable, one crimp contact was not tight so in some position it triggered the clicky probe contact.

DorjeDorf, 2022-02-25:
> I never noticed that, the magnets above more or less 80 degrees they start to lose strenght, but that is very hard to happen, at least with a silicone sock on the heat block.

Unless you run your mesh on a bed at 100-110C and have a small dive height. Then, the combined heat can impact accuracy. Usually it appears the longer the mesh runs. I know of a couple more people who observed the same effect. We were all meshing for ABS printing so the bed was above 100C. Dropping hotend temp around 130C was enough to do a full mesh :)

But here, seems it was the cable. So good news all around ;D

jlas1, 2022-03-02:
as it's solved, closing the issue.

HussamAlsahafi, 2023-03-17:
>

Which stepper motor ?

Closed 2022-03-02.

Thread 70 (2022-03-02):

V0.1 questions

dmnkhhn, 2022-03-02:
I’ve assembled the Klicky probe today and I have some questions/remarks that might help improve the already excellent instructions even further.
I had planned to use the automatic Z calibration and it wasn’t too obvious that this isn’t possible with the V0.1 besides clearly stating that it needs the nozzle to trigger the endstop. I was hoping the Klicky probing would do the job. It’s probably not really necessary with such a small bed but it sounded too good.

What’s the benefit of having the Klicky as the Z endstop?
If I use it that way, what are the next steps before I start my first print? Do I have to adjust my Z offset?

Is the z_offset value of the probe affected by printed parts tolerances and should be individually measured? What are the measuring points?

What does “probe_accuracy” and “probe_calibrate” do?

The instructions end with the “first test” section. What are the next steps? I have a working Klicky probe but I’m kind of lost what I can actually do with it.

Thank you for the work done and the work that will be done!

jlas1, 2022-03-02:
Let me try to answer your questions:
What’s the benefit of having the Klicky as the Z endstop?
Allows changing the bed surface or sheet without recalibrating.

If I use it that way, what are the next steps before I start my first print? Do I have to adjust my Z offset?
Yes, you need to adjust the Z offset with probe_calibrate.

Is the z_offset value of the probe affected by printed parts tolerances and should be individually measured? What are the measuring points?
The Z_offset is measured normally on the center of the bed, it is only measured when homing Z, it is not affected by what you are printing, more by at what temperature.

What does “probe_accuracy” and “probe_calibrate” do?
Check the klipper docs, probe_accuracy tests and displays the probe accuracy, probe_calibrate sets the probe z_offset.

The instructions end with the “first test” section. What are the next steps? I have a working Klicky probe but I’m kind of lost what I can actually do with it.
now that you have a working probe, use screws_tilt_calculate to help to adjust the bed screws, you can also do a bed mesh, both options are explained on the klipper docs, much better that by me here.

https://www.klipper3d.org/

dmnkhhn, 2022-03-03:
Thanks for taking the time to answer my questions, I hope I find the time in the next week to create a pull request with some additions to the instructions.

I will probably link to the parts of the Klipper docs in the relevant places so it's clear where to find more information. I wouldn't have looked at the Klipper docs to find more information about what I thought to be Klicky macros.

Maybe I explained wrong, I understood the `z_offset` (set to 14.5) as the hardware determined distance between the nozzle tip and the switch which might vary (magnets not fully pressed in, printed parts tolerances etc.)

jlas1, 2022-03-03:
The klicky macros, wrap around klipper functions, making sure that the probe is attached and taking care of the attach and dock it has no new functionality.
That being said, please submit a PR if you can, it would be welcomed.
Regarding the probe z_offset, it sometimes change a bit after a few prints, normally it is not a problem, if it is used as Z enstop, then you should calibrate it again after a few prints and printing hours.

Closed 2022-03-03.

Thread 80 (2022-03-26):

Need additional Nozzle Location Save in Probe_Calibrate

TechnicalMacaroon, 2022-03-26:
This could use an additional save_gcode_state original_nozzle_location in the probe_calibrate macro. Specifically between the _probe_calibrate and dock_probe lines.  I was getting an error from klipper because the nozzle wasn't in the expected location after starting the calibrate command.

jlas1, 2022-04-08:
Can you post your error, the probe_calibrate is very picky about unexpected toolhead moves during calibration.

TechnicalMacaroon, 2022-04-16:
My printer is currently down waiting for replacement parts but once they come in I'll re-edit my config and run it again to get you the exact error.

Closed 2022-06-23.

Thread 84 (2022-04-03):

Probe Not Attaching

Alexander-T-Moss, 2022-04-03:
I was finding the magnet in the dock was too strong, and thus the probe was not being pulled out. So I've made a [pull request](https://github.com/jlas1/Klicky-Probe/pull/85) with a modified dock that has the magnet slightly further away in the dock from the one on Klicky and found it to work better. I put a video below showing the issue.

https://user-images.githubusercontent.com/54496326/161437432-c8cde412-2bc7-4ae0-91a5-c66492121465.mov

jlas1, 2022-04-05:
i'll close this for now, if there is any issue with the new dock, we can open it again.

jangrewe, 2022-06-22:
I have the same issue with `Probes/UnklickyNG/STL/KlcikyNG_Probe_Dock.stl`, the current version. My quick fix to get it to work, so that i can print better fixes, was stuffing a bit of cardboard into the magnet hole to keep it further away from the probe's back magnet.

Closed 2022-04-05.

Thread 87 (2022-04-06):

LGX Lite

ModMike, 2022-04-06:
Can you add an LGX Lite mount to the V0.1 mix? Preferably one that works wit the existing carriage mount so we can use the metal ones and/or avoid having to re-belt the the printer?

Thank you.

jlas1, 2022-04-07:
Can you point me to the LGX Lite cowling that you are referring to?
The only one i know already has support for the integrated Klicky.

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

ModMike, 2022-04-07:
[Here you go](https://github.com/camerony/VoronCustom/tree/main/MiniASLGXerpaLiteMount). I don't like that back plate and was hoping to integrate with the metal [V0.1 MGNC carriage mount](https://www.aliexpress.com/item/1005003448901997.html?spm=a2g0o.order_list.0.0.21ef18027ZT92O).

I may take a crack at it myself but I think it would be nice to include and LGX lite extruder option in your GitHub.

jlas1, 2022-04-08:
I believe that that cowling is already in the repository, here https://github.com/jlas1/Klicky-Probe/blob/main/Printers/Voron/v0/v0_STL/Serpa_Mini_Dragon_Cowling_wKlicky.stl.
The LGX mount on top of it needs no modification.

jlas1, 2022-04-23:
gonna close this issue.

ModMike, 2022-04-23:
I went ahead and redesigned it the way I wanted. Thanks for blazing the trail!
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

jlas1, 2022-04-23:
Great that it worked out for you, with what probe did you end up using, i don't see the integrated klicky cutout on that image.

ModMike, 2022-04-23:
I went with my custom version of the zero click. Much smaller and cleaner all around.

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

jlas1, 2022-04-23:
looks good, thanks for the feedback.

ModMike, 2022-04-23:
Thank you for all your hard work. I would never had been able to do this without everything you did before.

GadgetAngel, 2022-04-23:
> I went with my custom version of the zero click. Much smaller and cleaner all around.
>
> 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

Where do you have this on the web?

ModMike, 2022-04-23:
It's not released yet. I'm still testing. I just finished printing my first set and am making adjustments. I will post when done.

ModMike, 2022-04-29:
In Beta, a few people printing, will release next weekend.

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

Rhastlyn, 2022-05-06:
> In Beta, a few people printing, will release next weekend.
>
> 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

Need any additional testers?  I'm thinking of this configuration for a rebuild and this looks promising!

Closed 2022-04-23.

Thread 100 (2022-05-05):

V0.1 Bed flex under probe pressure

gsezz, 2022-05-05:
When I'm using mesh bed leveling, my Z-offset is alsways about 0.1mm to close in the front, and 0.1mm to far in the back, with a perfect linear gradient back to front. No matter how scewed the bed actually is. I think this is because the froce needed to actuate the probe makes the bed bend more in the front than in the back.
I already upgraded to the kirigami bed, and used an switch with the lowest actuation force I could find (0.7N). Didin't anybody else have this problem?
Adding a lever to the switch brought it down to about 0.05mm difference front t o back, wich works, but still isn't pretty. And the lever is horrible for the overall accuracy.

jlas1, 2022-05-06:
I would suspect that you are using klicky on a V0(.1).
There were some users that had this difficulty, most don't see it.
However, there is a good news, i have a beta unklicky probe that triggers on 30g of force i can post it here, let me clean it up a bit.

jlas1, 2022-05-06:
Here it is, enjoy, [Unklicky_forV0.zip](https://github.com/jlas1/Klicky-Probe/files/8638677/Unklicky_forV0.zip) similar instructions on how to assemble here https://github.com/majarspeed/Unklicky.
The wires on the cable ducts should be without insulation

Closed 2022-05-06.

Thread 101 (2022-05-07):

Y homing for Y oriented probe ignores _HOME_Y

falo2k, 2022-05-07:
In the homing_override, the y homing section that triggers if attachmove_y ==0 doesn't use the same branching as further down the code.  As a result, for y oriented docks it will never call a _HOME_Y macro if one is defined, only ever calling a G28 Y0.  Confused the hell out of me while I was setting up my sensorless homing :)  Will submit a PR.

falo2k, 2022-05-07:
I'm now wondering if that section also needs to consider attachmove2_y when deciding on the y-first homing approach

jlas1, 2022-05-07:
good question, need to document the moves better.

falo2k, 2022-05-08:
I'd give it a go, but I feel like it would benefit from a gif, and I'm not that talented :)  Once I'm done swearing at my current build I'll have a look.

Is the thinking behind having a y home first for a y-oriented probe that it will avoid it accidentally picking up the probe early on XY homing?

jlas1, 2022-05-08:
it's more to avoid hitting the dock with the probe on initial homing.

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

falo2k, 2022-05-08:
Ah, gotcha - with the assumption that the dock is mounted along sides rather than back of the printer?  In which case it may need some rethinking then as for the case where I've got side entry but it's attached to the rear (euclid mount, mounted on rear gantry at back left, probe enters right to left) it can still hit the dock if it homes Y first (with a Y-based attachmove).  Maybe better as a home_y_before_x config flag rather than trying to infer it from the movements?

jlas1, 2022-06-23:
solved, now there is a variable (variable_override_homing) to control the homing order.

Closed 2022-06-23.

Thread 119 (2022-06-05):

Goal behind klicky probe

reparator, 2022-06-05:
Just a question:
What is the intention or the goal behind it? Which problem does this klicky probe solve? I could not really find that out in the documentation.
On a Voron you normally have a fixed inductive sensor for z-direction. Now it is variable. The tolerances should by higher with that. So what is the advantage?
Need some clarification.
Regards
Stefan

reparator, 2022-06-05:
After looking at that video: [https://www.youtube.com/watch?v=oQYHFecsTto&t=2s](url) now it is clear for me.

jlas1, 2022-06-06:
The goals or objectives are on the initial Readme.md, i have highlighted the most important when coming from an inductive sensor:

    drop in replacement for Omron TL-Q5MC2 or PL-08N2 (you don't need to replace the toolhead), replacement of BLtouch probes
    soldering not required
    minimal adjustments required
    be able to detect all the print surfaces
    be as close to the hotend tip as possible
    highly repeatable and accurate probes
    **less temperature variations**
    **no melting of its parts**
    **cheap to build**
    reuse spare parts if possible

Closed 2022-06-05.

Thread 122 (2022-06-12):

z-hob disabled, bed still crashes on low position when homing

ulk4, 2022-06-12:
I installed klicky-probe on a Qidi i-mate. Dock is mounted on upper front profile.
i-mate is a printer, where the bed falls down to bottom position (Z max), when motors are off.
I am using klicky-probe as Z-Endstop
When the printer is homing, it still tries to move the bed to a safe_z positon, but this is not possible, since the bed is already at lowest position. Z-hob is disabled.
I am not good in reading macros, so i could not really find out, where it happens and what is the problem.

The relevant configs are
klicky-variables.cfg
```
## only the modified lines
variable_safe_z:                 7
variable_enable_z_hop:       False
variable_max_bed_y:            200
variable_max_bed_x:            270
variable_z_endstop_x:            0
variable_z_endstop_y:            0
variable_docklocation_x:       266
variable_docklocation_y:        -7
Variable_dockmove_x:           -40
Variable_attachmove_x:           0
Variable_attachmove_y:         -30
```

printer.cfg
```
## only the changes made for klicky-probe

[include klicky-probe.cfg]

[stepper_z]
endstop_pin: probe:z_virtual_endstop
#position_endstop: 205.030			# removed for klicky-probe

[probe]
pin=^PE3
x_offset: 0
y_offset: -23
z_offset: 4.455
speed: 2.5
samples: 3
samples_result: median
sample_retract_dist: 2.0
samples_tolerance: 0.01
samples_tolerance_retries: 5
```

and the debug log from klipper terminal
```
20:48:21	probe: TRIGGERED
20:48:20	probe: TRIGGERED
20:48:18	Dock_Probe moving away from the dock to G0 X226 Y23 F4500
20:48:17	Dock_Probe moving from the dock to G0 X226 Y-7 F4500
20:48:17	Dock_Probe moving to the dock with G0 X266 Y-7 F3000
20:48:15	Dock_Probe moving near the dock with G0 X266 Y23 F12000
20:48:15	Dock_Probe going to dock probe
20:48:15	Dock_Probe Axis homed
20:48:15	Docking Probe
20:48:15	homing_override probe no longer required, docking probe
20:48:14	_Home_Z toolhead too low, raising it to 7.0mm
20:47:43	_Home_Z Homing Z G28 Z
20:47:43	_Home_Z moving to Z endstop position G0 X134.0 Y124.5 F12000
20:47:43	_Home_Z Axis homed
20:47:43	probe: open
20:47:42	Attach_Probe moving to a safe Z position: G0 Z7 F1200
20:47:41	Attach_Probe moving from the dock to G0 X266 Y23 F4500
20:47:41	Attach_Probe moving to the dock with G0 X266 Y-7 F3000
20:47:41	Attach_Probe moving to the dock with G0 X266 Y-7 F3000
20:47:39	Attach_Probe moving near the dock with G0 X266 Y23 F12000
20:47:38	Attach_Probe toolhead too low, raising it by 7mm, duplicate?
20:47:38	Attach_Probe toolhead too low, raising it by 7mm
20:47:37	Attach_Probe going to attach probe
20:47:37	moving to a safe Z distance
20:47:37	Attaching Probe
20:47:37	homing_override probe configured as a virtual Z endstop attaching probe
20:47:37	homing_override backing off Y endstop, G0 Y193.0 F12000
20:47:32	homing_override Homing Y G28 Y0
20:47:32	homing_override backing off X endstop, G0 X258.0 F12000
20:47:26	homing_override Homing X G28 X0
20:47:26	homing_override toolhead too low, raising it by 0mm
20:47:26	homing_override Z not homed, setting position as X=Y=Z=0
20:47:26	homing_override z_hop disabled
20:47:25	homing_override goint to home all axes
20:47:25	probe: TRIGGERED
20:47:25	Homing Z
20:47:25	Homing Y
20:47:25	Homing X
20:47:25	Z not homed, forcing full G28
20:47:25	G28
```
I think the bed move in positive Z direction is happening at 20:47:38, but it is scrolling quite fast.

Btw, when I apply the klicky-probe manually before homing, it is working without the collision move.

For the moment as a workaround, I lowered safe_z to only 7mm and placed some foam on the bottom of the printer, so the bed does not fall down all the way and the collision is a soft one.
Any idea, why `variable_enable_z_hop:       False` is not working as expected?

And last not least, Docking, attaching and bed mesh calibration are working fine :-)

jlas1, 2022-06-23:
I see the issue, it needs to be able to move to attach if the Z is too low.
Try this macro:
https://raw.githubusercontent.com/jlas1/Klicky-Probe/z_hop_tests/Klipper_macros/klicky-variables.cfg
It should work as expected, it is on a new branch.

ulk4, 2022-06-26:
I used the macro [https://raw.githubusercontent.com/jlas1/Klicky-Probe/z_hop_tests/Klipper_macros/klicky-macros.cfg](url) from
z-hob_tests branch.
Now, when the printer is homing, before homing x any y, the bed is moved up by `variable_safe_z`. Later on, before attaching the probe, the bed is lowered again the same amount, which is now possible. I guess this is the expected behaviour.
At least, it does not try to move the bed downwards anymore in the beginning, when it is already at bottom position.
Looks good to me, I can take out the foam again :-).
Thanks.

jlas1, 2022-06-27:
Can you enable the debug variable on klicky-variables.cfg and do a homing please?
Would like to find out why is it moving like that.

ulk4, 2022-06-27:
Sure. Here is the debug log

**07:42:53	probe: TRIGGERED
07:42:52	probe: TRIGGERED
07:42:50	Dock_Probe moving away from the dock to G0 X226 Y23 F4500
07:42:49	Dock_Probe moving from the dock to G0 X226 Y-7 F4500
07:42:49	Dock_Probe moving to the dock with G0 X266 Y-7 F3000
07:42:47	Dock_Probe moving near the dock with G0 X266 Y23 F12000
07:42:47	Dock_Probe going to dock probe
07:42:47	Dock_Probe Axis homed
07:42:47	Docking Probe
07:42:47	homing_override probe no longer required, docking probe
07:42:46	_Home_Z toolhead too low, raising it to 7.0mm
07:42:21	_Home_Z Homing Z G28 Z
07:42:21	_Home_Z moving to Z endstop position G0 X134.0 Y124.5 F12000
07:42:21	_Home_Z XY Axis homed
07:42:21	probe: open
07:42:21	Attach_Probe moving to a safe Z position: G0 Z7 F1200 from -0.029827
07:42:19	Attach_Probe moving from the dock to G0 X266 Y23 F4500
07:42:19	Attach_Probe moving to the dock with G0 X266 Y-7 F3000
07:42:19	Attach_Probe moving to the dock with G0 X266 Y-7 F3000
07:42:18	Attach_Probe moving near the dock with G0 X266 Y23 F12000
07:42:16	Attach_Probe toolhead too low, raising it by 7mm, duplicate?
07:42:16	Attach_Probe toolhead too low, raising it by 7mm
07:42:16	Attach_Probe going to attach probe
07:42:16	moving to a safe Z distance
07:42:16	Attaching Probe
07:42:16	homing_override probe configured as a virtual Z endstop attaching probe
07:42:10	homing_override Homing Y G28 Y0
07:42:03	homing_override Homing X G28 X0
07:42:03	homing_override toolhead too low, raising it by 0mm
07:42:03	homing_override Z not homed, setting position as X=Y=0 Z=7
07:42:03	homing_override z_hop disabled
07:42:03	homing_override goint to home all axes
07:42:03	probe: TRIGGERED
07:42:03	Homing Z
07:42:03	Homing Y
07:42:03	Homing X
07:42:03	Z not homed, forcing full G28
07:42:03	G28**

I think it happens at **07:42:03	homing_override toolhead too low, raising it by 0mm**, even when it says it's moving by 0mm. Bed is raised by safe_z.
My guess is, kinematic position is set to Z=7 and then the bed is moved absolutely to safe_z, which is 0 at that time. This results in the first bed raise. BUT: it is only my guess, i'm not good in reading and understanding macros.

jlas1, 2022-06-27:
Can you try now with the main macros?
https://raw.githubusercontent.com/jlas1/Klicky-Probe/main/Klipper_macros/klicky-macros.cfg

You are better at macros than you think, your guess is right.

ulk4, 2022-06-27:
Perfect !
No unnecessary moves any more.
Here is the log with unhomed printer.

```
13:04:05	probe: TRIGGERED
13:04:04	probe: TRIGGERED
13:04:02	Dock_Probe moving away from the dock to G0 X226 Y23 F4500
13:04:00	Dock_Probe moving from the dock to G0 X226 Y-7 F4500
13:04:00	Dock_Probe moving to the dock with G0 X266 Y-7 F3000
13:03:59	Dock_Probe moving near the dock with G0 X266 Y23 F12000
13:03:59	Dock_Probe going to dock probe
13:03:59	Dock_Probe Axis homed
13:03:59	Docking Probe
13:03:59	homing_override probe no longer required, docking probe
13:03:58	_Home_Z toolhead too low, raising it to 7.0mm
13:03:33	_Home_Z Homing Z G28 Z
13:03:33	_Home_Z moving to Z endstop position G0 X134.0 Y124.5 F12000
13:03:33	_Home_Z XY Axis homed
13:03:33	probe: open
13:03:31	Attach_Probe moving from the dock to G0 X266 Y23 F4500
13:03:31	Attach_Probe moving to the dock with G0 X266 Y-7 F3000
13:03:31	Attach_Probe moving to the dock with G0 X266 Y-7 F3000
13:03:29	Attach_Probe moving near the dock with G0 X266 Y23 F12000
13:03:29	Attach_Probe going to attach probe
13:03:29	Attaching Probe
13:03:29	homing_override probe configured as a virtual Z endstop attaching probe
13:03:21	homing_override Homing Y G28 Y0
13:03:18	homing_override Homing X G28 X0
13:03:18	homing_override Z not homed, setting position as X=Y=0 Z=7
13:03:18	homing_override z_hop disabled
13:03:18	homing_override goint to home all axes
13:03:18	probe: TRIGGERED
13:03:18	Homing Z
13:03:18	Homing Y
13:03:18	Homing X
13:03:18	Z not homed, forcing full G28
13:03:18	G28
```

Thanks for your help.
Btw, do you want to add the custom klicky-probe files for the Qidi i-mate to your github? Don't know, if it makes sense, since you need several modifications to the printer in advance. (klipper and a new printhead).

MrReflex89, 2023-12-27:
Unfortunately, after more than a year the link no longer works. Can someone please tell me where I can find this cfg because I have the same problem with the same printer and have little knowledge of macros to change them myself.
( don´t work: https://raw.githubusercontent.com/jlas1/Klicky-Probe/main/Klipper_macros/klicky-macros.cfg :( )

MrReflex89, 2023-12-27:
Hello everyone, I also have the same problem that if the bed is on the old limit switch and continues to move freely at the beginning, this leads to a collision. I have another problem when a print is finished that the printer switches to save z 10, which would cause a collision with the printed part. Of course I could set the safety height to 200, but when touching it at the start of the print program it would unnecessarily move up and down twice. does anyone have an idea what I can do? I have the latest macros and configs.

klicky-variables.cfg:
[gcode_macro _User_Variables]
variable_verbose:             True    # Enable verbose output
variable_debug:              False    # Enable Debug output
variable_travel_speed:         200    # how fast all other travel moves will be performed when running these macros
variable_move_accel:          1000    # how fast should the toolhead accelerate when moving
variable_dock_speed:            50    # how fast should the toolhead move when docking the probe for the final movement
variable_release_speed:         75    # how fast should the toolhead move to release the hold of the magnets after docking
variable_z_drop_speed:          20    # how fast the z will lower when moving to the z location to clear the probe

variable_safe_z:         	    10    # Minimum Z for attach/dock and homing functions     #orig: 25
# if true it will move the bed away from the nozzle when Z is not homed
variable_enable_z_hop:        False    # set this to false for beds that fall significantly under gravity (almost to Z max)   #orig: True

variable_max_bed_y:            200    # maximum Bed size avoids doing a probe_accuracy outside the bed
variable_max_bed_x:            270    # maximum Bed size avoids doing a probe_accuracy outside the bed

# if a separate Z endstop switch is in
# use, specify the coordinates of the switch here (Voron).
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

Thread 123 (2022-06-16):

Bed Crashing to bottom on V0.1

jeronbernal, 2022-06-16:
I would love any help i can get on this, i feel like i'm completely missing something >_>;;

When testing after homing X/Y the bed will try to lower 25, then lower again. then give me a Move out of Range :

08:56:44
Move out of range: -879.000 14.000 25.000 [0.000]
08:56:44
Move out of range: -879.000 14.000 25.000 [0.000]
08:56:40
Resetting Z position to zero, duplicate?
08:56:40
moving to a safe Z distance
08:56:40
Resetting Z position to zero
08:56:40
Attaching Probe

My klicky_variable.cfg :

[gcode_macro _User_Variables]
variable_verbose:               True  # Enable verbose output
variable_travel_speed:          100   # how fast all other travel moves will be performed when running these macros
variable_dock_speed:            50    # how fast should the toolhead move when docking the probe for the final movement
variable_release_speed:         55    # how fast should the toolhead move to release the hold of the magnets after docking
variable_z_drop_speed:          20    # how fast the z will lower when moving to the z location to clear the probe

variable_safe_z:         	    25    # Minimum Z for attach/dock and homing functions
# if true it will move the bed away from the nozzle when Z is not homed
variable_enable_z_hop:        True    # True v0

#Dock move
Variable_dockmove_x:             0    # Final toolhead movement to release
Variable_dockmove_y:            40    # the probe on the dock
Variable_dockmove_z:             0    # (can be negative)

#Attach move
Variable_attachmove_x:          30    # Final toolhead movement to Dock
Variable_attachmove_y:           0    # the probe on the dock
Variable_attachmove_z:           0    # (can be negative)

variable_max_bed_x:             120   # maximum Bed size avoids doing a probe_accuracy outside the bed
variable_max_bed_y:             120   # maximum Bed size avoids doing a probe_accuracy outside the bed

# if a separate Z endstop switch is in
# use, specify the coordinates of the switch here (Voron).
# Set to 0 to have the probe move to center of bed
variable_z_endstop_x:         0
variable_z_endstop_y:         0

#Check the printer specific documentation on klipper Dock/Undock configuration, these are dummy values
#dock location
variable_docklocation_x:      121    # X Dock position
variable_docklocation_y:      14    # Y Dock position
variable_docklocation_z:      -128    # Z dock position (-128 for a gantry/frame mount)

#The following variables are used if the dock is deployed and retracted via a servo motor
variable_enable_dock_servo:  False    # Set to true if your klicky dock is servo-controlled
variable_servo_name:        'NAME'    # The name of the dock servo defined in printer.cfg under [servo]
variable_servo_deploy:          10    # This EXAMPLE is the value used to deploy the servo fully
variable_servo_retract:         11    # This EXAMPLE is the value used to retract the servo fully (initial_angle in [servo] config)
variable_servo_delay:          250    # This is a delay to wait the servo to reach the requested position, be carefull with high values

#Dock move, final toolhead movement to release the probe on the dock
#it's a relative move
Variable_dockmove_x:          1000
Variable_dockmove_y:             0
Variable_dockmove_z:             0

#Attach move. final toolhead movement to attach the probe on the mount
#it's a relative move
Variable_attachmove_x:        1000
Variable_attachmove_y:           0
Variable_attachmove_z:           0

#Umbilical to help untangle the umbilical in difficult situations
variable_umbilical:          False    # should we untangle the umbilical
variable_umbilical_x:           15    # X umbilical position
variable_umbilical_y:           15    # Y umbilical position

# location to park the toolhead
variable_park_toolhead:      False    # Enable toolhead parking
variable_parkposition_x:       125
variable_parkposition_y:       125
variable_parkposition_z:        30

variable_version:                1    # Helps users to update the necessary variables, do not update if the variables above are not updated

#Below this remark, you normally do not need to configure
#Attach move2
Variable_attachmove2_x:          0    # intermediate toolhead movement to attach
Variable_attachmove2_y:          0    # the probe on the dock
Variable_attachmove2_z:          0    # (can be negative)

variable_home_backoff:          10    # how many mm to move away from the endstop after homing

variable_override_homing:        ''   # configures what axis to home first
                                      #  '' = default klicky behavior (tries to avoid the hitting the dock
                                      # 'X' = forces X to home first
                                      # 'Y' = forces Y to home first

# Do not modify below
gcode:
    {% set Mx = printer['configfile'].config["stepper_x"]["position_max"]|float %}
    {% set My = printer['configfile'].config["stepper_y"]["position_max"]|float %}
    {% set Ox = printer['configfile'].config["probe"]["x_offset"]|float %}
    {% set Oy = printer['configfile'].config["probe"]["y_offset"]|float %}
    {% set Oz = printer['configfile'].config["probe"]["z_offset"]|float %}

    # If x, y coordinates are set for z endstop, assign them
    {% if z_endstop_x != 0 or z_endstop_y != 0 %}
        SET_GCODE_VARIABLE MACRO=_Probe_Variables VARIABLE=z_endstop_x VALUE={ z_endstop_x }
        SET_GCODE_VARIABLE MACRO=_Probe_Variables VARIABLE=z_endstop_y VALUE={ z_endstop_y }

    # if no x, y coordinates for z endstop, assume probe is endstop and move toolhead to center of bed
    {% else %}
        SET_GCODE_VARIABLE MACRO=_Probe_Variables VARIABLE=z_endstop_x VALUE={ (Mx * 0.5) - Ox }
        SET_GCODE_VARIABLE MACRO=_Probe_Variables VARIABLE=z_endstop_y VALUE={ (My * 0.5) - Oy }
    {% endif %}

jlas1, 2022-06-16:
Hi, you need to modify the dockmoves:
Variable_dockmove_x: 1000
Variable_dockmove_y: 0
Variable_dockmove_z: 0

#Attach move. final toolhead movement to attach the probe on the mount
#it's a relative move
Variable_attachmove_x: 1000
Variable_attachmove_y: 0
Variable_attachmove_z: 0

For a V0.1the correct is here:
https://github.com/jlas1/Klicky-Probe/tree/main/Printers/Voron/v0#step-5-klipper-configuration

#Dock move
Variable_dockmove_x:             0    # Final toolhead movement to release
Variable_dockmove_y:            40    # the probe on the dock
Variable_dockmove_z:             0    # (can be negative)

#Attach move
Variable_attachmove_x:          30    # Final toolhead movement to Dock
Variable_attachmove_y:           0    # the probe on the dock
Variable_attachmove_z:           0    # (can be negative)

jeronbernal, 2022-06-17:
Thank you, i copied it over but i didn't get rid of the same attachmove and
dockmove below. it works perfectly now! thank you so much for the klicky,
it's amazing to watch in use.

I had another question regarding docking and attaching between homing and
bed mesh prior to a print.  How can i prevent the klicky from docking
between G28 and bedmesh?   Thank you!!

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

jlas1, 2022-06-17:
Try this:
G28 X Y
ATTACH_PROBE_LOCK
G28 Z
BED_MESH_CALIBRATE
DOCK_PROBE_UNLOCK

jlas1, 2022-07-04:
closing this issue, can always be opened again

Closed 2022-07-04.

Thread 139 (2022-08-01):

Missing body STL for 3mm magnets (KlickyNG)

shlagwuk, 2022-08-01:
Hi,
With 3mm height magnets, the body STL is too small and the back part often breaks.

In the CAD file, there is a 3mm body that works better! Is it possible to add it to the rep files ?

In the screenshot below, the 3mm file from cad is enlightened, and the bigger space is visible.
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

poon-holder, 2022-08-05:
The Mini AB cowing mount is also a bugger, keeps knackering the part when inserting the magnets. Are the designs meant for ABS?

Brassn, 2022-08-08:
Sadly I cannot find the better working 3mm body part you mentioned in the CAD step file. Is it possible that you had an older version of the CAD files laying around? Current version is v9.

Also confusing is that BOM clearly prefers 3mm magnets but the parts make it seem like 2.75mm was standard and 3mm was a (less supported?) alternative.

jlas1, 2022-11-22:
Try with the latest parts it should work better.

Closed 2022-11-22.

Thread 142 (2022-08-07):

Firmware wont start

dkuchay, 2022-08-07:
Spent two weeks reading this guide and decided last night to execute. I have had a voron 2.4 350 for over a year now and I am unable to complete this guide. I do not know gcode and dont expect I will. Would have executed earlier but the way this guide is written is like a scavenger hunt. Takes several passes before one knows what to omit. Get as far as the gcode commands but they dont locate the print head anywhere near the dock mount on a 350mm. The plastic parts seem off as the part that is attached to the print head crashes into the part on the dock mount forcing the whole assembly down 10-15mm. Yes, it's adjusted up all the way in the print head.  Something will break after a few uses based on how far this flexes after impacting the mount. This is static as it mounts to the gantry.  Using purge bucket and just held the non purge bucket part up next to and there is a height difference. Looks like I have to not use a purge bucket to get the correct height. Crap.  Would have been a lot easier if this was a static guide on one page (with all extra reading links at the bottom). This reads like a reddit post. Would have been better if it read like a wiki. gcode commands that didnt need interpretation as I dont have the needed knowledge. Was able to get x and y homed but once I told it to use 100, 100 for safe z axis firmware wouldnt restart. No indications as to why. If it won't start logs don't reveal. Although I know where to look as I have 20 years experience with linux and can build a kernel without issue this guide is not able to be completed as it stands without intimate knowledge of gcode. Reformatting SD card and going back to magnetic probe.  STL for purge bucket dock mount looks to be the reason for the crashing as it has delta in height compared to non purge bucket gantry dock part. FYI. Thanks for the effort.

dkuchay, 2022-08-09:
Close this. I have it working now. Had to find one of your older guides that only dealt with the klicky-probe.cfg file only and then bounced into current for the parts I needed. I have to wonder if a static how-to for each printer would have been easier.

Closed 2022-08-09.

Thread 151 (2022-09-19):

Back magnet in probe is 0.2mm higher than 2 other magnets (that are attached to microswitch)

rstanislav, 2022-09-19:
Looking at the sliced part i can see that back magnet is 1 layer higher (0.2mm), so when assembled it causes very small tilt by 0.2mm, is it supposed to be like this ?(on the left side of the photo you can see there is 2 layers of wall already around magnet, and on the right - only 1 layer of wall)
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

jlas1, 2022-11-22:
you are correct, it was 0.113 mm lower, corrected that in CAD, when i push that version, it will be correct.
With that said, the glue should prevent it from being too deep inside.

Closed 2022-11-22.

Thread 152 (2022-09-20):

Upgrading to new Klipper macros leads to printer no longer auto-attaching/auto-docking

kubark42, 2022-09-20:
I recently upgraded the Klipper macros. I copied over all the old settings, as instructed. Everything works fine, but now I have to manually click the `Attach` and `Dock` macros in MainSail. Clicking the QGL (Quad Gantry Leveling) or the Bed Mesh Calibration no longer automatically attach the probe at the beginning and dock it at the end.

Perhaps of importance: when I click the QGL button, the print head immediately travels to the first probe location. It then halts there with a `Probe triggered prior to movement`.

kubark42, 2022-09-20:
Aaand, figured it out. This was due to documentation confusion, where https://github.com/jlas1/Klicky-Probe/tree/main/Klipper_macros#updating-from-an-earlier-version mentions changing variables in `klicky-probe.cfg`, but the variables listed are all in `klick-variables.cfg`.

It turns out that *both* files need to be updated, as `klicky-probe.cfg` contains the includes which need to be set correctly. In my case,

```
#Simple way to include all the various klicky macros and configurations
# the current home for this configuration is https://github.com/jlas1/Klicky-Probe, please check it

#[include ./klicky-specific.cfg]                #place to put other configurations specific to your printer
[include ./klicky-variables.cfg]                #Required
[include ./klicky-macros.cfg]                   #Required
[include ./klicky-bed-mesh-calibrate.cfg]      #bed mesh, requires klipper configuration
#[include ./klicky-screws-tilt-calculate.cfg]   #help adjust bed screws automatically
[include ./klicky-quad-gantry-level.cfg]       #level 4 Z motors
#[include ./klicky-z-tilt-adjust.cfg]           #level 2 or 3 Z motors
```

Closed 2022-09-20.

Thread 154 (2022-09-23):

Safe Z doesn't appear to be working on an x/y home

simpat1zq, 2022-09-23:
Voron 2.4R2. Before I setup the Klicky macros, I was using safe_z_home, which is now commented out per the instructions.

However, when I do an x/y home, it is not raising the z, which can potentially cause issues if the nozzle is close to the bed. How do I get that feature back where it raises the z when homing x/y?

Also, if I just home Z, it raises the gantry, does an x/y home, and then a z home. So that works the way it should. However, if I turn the motors off, it _should_ forget the coordinates, but that doesn't appear to happen. Even after turning the motors off, if I do a Z home, it does the x/y home without raising the z. When the motors turn off the printer should assume it no longer knows where the toolhead is, and that doesn't appear to be happening when using the Klicky macros.

jlas1, 2022-11-18:
Can you check the latest macro version and advise if the bug is still there?
also, please include your klicky-variables.cfg

jlas1, 2022-11-25:
should be solved now, if necessary please reopen.

Eiranya, 2023-01-11:
> should be solved now, if necessary please reopen.

I used Latest macro,if the xyz axes are already homed,run the full G28 command x/y axes will directly goint to home without raising the z,but if it close to the heatbed  when toolhead run to z endstop position the toolhead will hit the z endstop. Moves the Z to safe_z distance only on the first G28 after motors losing power.

Closed 2022-11-25.

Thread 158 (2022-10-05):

[KlickyNG] AB/SB Mount Cracking When Tightening M2x10 Screws

ndanyluk, 2022-10-05:
Hi, love Klicky and happy to get it installed on my SW, but wanted to flag an issue I saw during assembly.

It seems that the AB/SB mount suffers strain when tightening the M2 screws that hold the magnets in place. On four separate attempts, I managed to crack the AB/SB mount when tightening the right hand screw.  Each time I had not tightened the screw the entire way yet and had to be extremely delicate with tightening on my final successful attempt.

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

That thin line across the side is from the plastic splitting.  I used standard Voron part settings (4x perimeters, 5x solid top/bottom layers, 40% infill) but it may help to print with lower infill in that section so the screw doesn't force the plastic apart.

ndanyluk, 2022-10-06:
OK quick update - after 10 repeated failures with varying settings (different flow, xy compensation, drilling out the hole with a 1/16th bit) I decided to jump into the slicer and see what this looks like.

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

It seems that with the spec'd settings, this area becomes a solid block of plastic with some gap fill.  It might do better with arachne, but in my case the self-tapping screws exert too much force on these outer walls and split the plastic.  Probably a mix of poor layer adhesion and just the wrong tolerance on the screws, but figured I'd share my experience.  Would probably recommend opening this hole up by .1mm but I'm out of filament to test with unfortunately.

Ramalama2, 2022-10-26:
You have to use definitively arachne. I don't know how the world worked before Arachne anymore 😂

Backstory first:
Tbh, tolerances aren't that easy as you think, designers like me are trying to find a middle ground that works for most people.
But primarily the designer does what works best for himself, because he can selfprint the parts and test directly.
The part with "what works best for most" comes then a lot later, once people start to complain, the first ones then get ignored and if there are more then the tolerances get adjusted.

Now the problem with tolerances relies heavily on flowrate, calibrated extruder, filament width, nozzle...
And everyone or every printer is a little bit different in that aspect.
Including that those self tapping screws are all a little bit different either.
On your particular problem the fan speed, layerhight play a big role either, because it's like an overhang, that hole.

Now back to arachne, the slicers before Arachne with the old engine, can differ a hole up to 0.1mm im worst cases even up to 0.2mm, i seen that and it's extremely horrible on very small holes especially.
Depending on how far they are away from outer wall etc.
I myself try to design holes and the distance of those holes always in multiple of 0.4 or 0.2mm.
And i do that only for the compatibility for the old engine.
For Arachne, i can basically give a fuck to everything and design how i like, because Arachne does thicker/thinner lines and that helps extremely to keep the parts how they are meant.

And as last point, your print looks a bit crappy to me, like not well calibrated etc.... Especially pressure advance.

So as conclusion after the whole writeup, try first to switch to Arachne and tune your printer a bit.
Then if we are lucky it's probably solved for this AND for future prints!

Cheers

jlas1, 2022-11-21:
You may be over-extruding a bit, this happened on the initial revisions, but it seems that it works for most people as is right now, hard to change that with only 1 report.
You can also increase the hole size of that part on a CAD software, should be easy, but if you need, DM me in discord or reopen this issue.

Best Regards and thanks for the issue.

grimlokason, 2023-01-22:
Hello,

I'm having the same issue, even by under extruding.
I'm also having hard time with a 2 mm screw tap
I noticed that your hole are 1.5mm while it should be 1.6 according what i saw for M2 screw ( http://www.carbidedepot.com/formulas-tap-metric.htm )

i'll try with an hole of that side and come back to you

Closed 2022-11-21.

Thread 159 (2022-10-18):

klicky-macros.cfg: Probe positions are truncated to nearest int (why???)

idonasch, 2022-10-18:
In klicky-macros.cfg  all references to docklocation_* are cast/filtered to the nearest integer. My dock was off by 0.4mm which caused the attach_probe to fail. The probe always was skewed by a couple degrees and didn't made contact.
Is there a reason that I might have missed? Wouldn't round() be more appropriate if conversion is needed at all?
Anyways I would recommend to do any necessary conversions up in the {% set  ... %} section.

I had to pry the mount over by 0.5mm to get it working.

jlas1, 2022-11-21:
I'll check how hard is to correct

jcfain, 2023-10-08:
Just popping in to say I noticed this last night and I agree it should not be casting to an int. Luckily my dock landed close enough to a whole number (43.15) where it still works.

Closed 2024-08-06.

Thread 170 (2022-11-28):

Trying to set up probe as Z endstop. Z homing sequence does not pick up probe.

cullinaire, 2022-11-28:
I got the klicky installation finished and working properly with the normal Z endstop per stock Voron. Next I wanted to use the probe as Z endstop so I followed the linked documentation. Then came the problems: at Z home, instead of attaching the probe, the printhead would go to the dock and act like it's detaching the probe even though it never had a probe in the first place. So I set variable_dock_on_zhome to false.
That fixed the docking issue, but now instead of attaching the probe, at Z home it just stops with error "Endstop z still triggered after retract". So I then inverted the polarity of the endstop pin. Now the probe is not picked up at Z home, and attempts to just home it anyways forcing me to emergency stop to prevent the nozzle from crashing.
The only way I have ever successfully done a Z home is by manually homing X and Y, then manually attaching the probe (which required me to reset polarity of the probe endstop pin (which now shows as normally triggered) and running the Z home.
[klicky-variables (1).zip](https://github.com/jlas1/Klicky-Probe/files/10101523/klicky-variables.1.zip)

cullinaire, 2022-11-29:
Error in printer.cfg: there was a space between "probe: z_virtual_endstop" in the stepper_z endstop pin section. Removed the space so it reads "probe:z_virtual_endstop" and all is fixed.

jlas1, 2022-11-29:
just would like to note that it's solved in the code now.

cullinaire, 2022-11-29:
Thanks!

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

--
Best,

Weseung Hwang

Closed 2022-11-29.

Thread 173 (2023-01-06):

Switchwire Drive Arm STL's are backwards

andypm1982, 2023-01-06:
the STL's i downloaded show the magnet holes are reversed on the arms. the magnet end up being on the wrong side of the arms.

How can i resolve this?

Thanks.

seansch, 2023-01-21:
I've been scratching my head about this too, the arms I printed don't match up with what is in the Switchwire installation guide pictures.

seansch, 2023-01-21:
I went ahead with the assembly with the printed parts from the SW STL folder and they are correct.

But for reference what I was comparing to were the images here:
 https://github.com/jlas1/Klicky-Probe/blob/7a31e885b36d98702cce62d8181da80eb7d446b5/Printers/Voron/Switchwire/Photos/20220601_122838.png
https://github.com/jlas1/Klicky-Probe/raw/7a31e885b36d98702cce62d8181da80eb7d446b5/Printers/Voron/Switchwire/Photos/20220601_123056.png
https://github.com/jlas1/Klicky-Probe/raw/7a31e885b36d98702cce62d8181da80eb7d446b5/Printers/Voron/Switchwire/Photos/back_servo.png
https://github.com/jlas1/Klicky-Probe/raw/7a31e885b36d98702cce62d8181da80eb7d446b5/Printers/Voron/Switchwire/Photos/IMG_20220606_1932032_2.jpg

These images show the magnets in different locations than the current printed parts.

jlas1, 2023-01-21:
Sorry about this, the parts were updated, to avoid having the magnets being pulled from the holes, but the images have not been updated.

andypm1982, 2023-01-21:
That’s fine and I get that but I’m finding the depth of the hole is to shallow now the magnets are reversed. The magnets even with triple stacked isn’t holding the arm in place. I don’t know whether that’s just when the servo isn’t powered or not. I need to test.

seansch, 2023-01-21:
I completed the assembly last night and didn't have any issues with the magnets holding the arms together, with or without the servo attached. Are you sure you have the arms attached correctly? The "small" holes should be facing each other, between the arms, ensuring that the polarity of the magnets is pulling the arms together.

Closed 2023-01-21.

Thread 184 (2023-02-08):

Trident raises bed in wrong direction on Z home, causing crash

MiniMook, 2023-02-08:
Hello,

I built a new Trident from an LDO kit, and I was running into an issue migrating to Klicky.

When I comment out the `safe_z_home` section in the LDO-provided config and migrate to Klicky, following the instructions laid out at https://github.com/jlas1/Klicky-Probe/blob/main/Printers/Voron/v1.8_v2.4_Legacy_Trident/README.md , the bed direction switches when first running G28 for X, Y, and Z. This is the step where the bed should lower by about 25mm to give the nozzle and probe room to move. Of course, since the printer homes X first, Klicky doesn't bother attaching the probe at this point.

Instead, the bed moves _up_ (as in the Z-height decreases) instead of moving _down_. This only happens with my Klicky configuration, that is, disabling Klicky and going back to the old config moves the bed in the correct direction. If the bed is already greater than 25mm away from the nozzle, then there are no issues, the bed moves up but stays away from the printhead, then X, Y, and Z home properly. Klicky even attaches and docks properly as well, since I calibrated everything else. Once Klicky is attached, I can run the z tilt adjust macros and move the axes manually and all of that works just fine. Therefore I do not believe this to be a motor wiring issue.

I've narrowed the issue to https://github.com/jlas1/Klicky-Probe/blob/main/Klipper_macros/klicky-macros.cfg#L663 which is the line that runs the command causing my problem.

Could someone help me figure out what is going on here, and maybe fix the issue?

MiniMook, 2023-02-09:
This issue was resolved through the klicky config items:

```
variable_safe_z:         	    25    # Minimum Z for attach/dock and homing functions
# if true it will move the bed away from the nozzle when Z is not homed
variable_enable_z_hop:        True    # set this to false for beds that fall significantly under gravity (almost to Z max)
```

I needed to set `variable_enable_z_hop` to `true` to get the correct direction of motion. The README.md file may need updating, because for this line it says:

```
variable_enable_z_hop           # set this to false for beds that fall significantly under gravity (almost to Z max)
```

FlyingT, 2023-02-19:
Same issue, Fysect Kit
wondered why I should disable it but followed the instructions provided since why would they be wrong
Result: https://ibb.co/nmHWgHK

Obviously I see this AFTER destroying my bed and finding the same solution myself ... :(
@jlas1 THIS NEEDS TO BE FIXED ASAP, YOUR README IS KILLING PRINTBEDS

julianschill, 2023-02-19:
I think I narrowed down the problem:
Assuming enable_z_hop is False and safe_z is set to 25:

Here: https://github.com/jlas1/Klicky-Probe/blob/8290f00a6605a0904dd56109a5e595617daae02b/Klipper_macros/klicky-macros.cfg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
kinematic_position gets set to 25 and safe_z_home to 0.

Here:
https://github.com/jlas1/Klicky-Probe/blob/8290f00a6605a0904dd56109a5e595617daae02b/Klipper_macros/klicky-macros.cfg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
The current position gets set to Z=25

And here:
https://github.com/jlas1/Klicky-Probe/blob/8290f00a6605a0904dd56109a5e595617daae02b/Klipper_macros/klicky-macros.cfg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

A G0 Z0 gets executed, which moves the nozzle 25mm towards the bed.

MiniMook, 2023-02-19:
> The current position gets set to Z=25

Sounds like that is incorrect, I think when no axes are homed, the kinematic position should be assumed to be Z=0 so that there is no possibility of moving the bed upwards.

the only situation in which this would be bad is if the real Z is >= 275mm and adding 25mm of travel would cause a crash towards the bottom of the chamber.

jlas1, 2023-02-20:
that's interesting, let me have a look,that's not supposed to happen.

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

FlyingT, 2023-02-20:
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

Small note:
All "default" Trident, independend of bed size, have A Z of 250 not 300

btoconnor, 2023-03-29:
Very new to klipper and klicky, but I just ran into this issue as well.  The comment around the code in question claims `On the first G28 after motors losing power, moves the Z to safe_z distance, if z_hop is enabled`.  I had `variable_enable_z_hop` to `False` and I'm not using klicky as an end stop - I was surprised to see that the klicky macro would make movements on z in any direction in this scenario.  I feel like the command `G0 Z{safe_z} F{z_drop_feedrate}` on [L663](https://github.com/jlas1/Klicky-Probe/blob/main/Klipper_macros/klicky-macros.cfg#L663) should be gated by enable z hop and/or klicky being a virtual end stop? I'd prefer the z axis to not move at all unless it's homed by the z endstop switch.

srberard, 2023-12-10:
I have a v1.8.  I too had to set the variable_enable_z_hop to true to get the correct direction of motion. The code appears to function properly, this is just a documentation bug IMHO.  Once set to true, everything works as it should.

ComradeHappy, 2023-12-30:
I had this issue too. Setting varaible_enable_z_hop to true did not work for me. This cfg file seems to work. Once more testing is done it will be uploaded.

Thanks @jlas1

[klicky-macros.cfg.zip](https://github.com/jlas1/Klicky-Probe/files/13796636/klicky-macros.cfg.zip)

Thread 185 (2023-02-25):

During homing, probe is still triggered after pickup. BUT doing manual pickup, it works fine.

DragonFlyer007, 2023-02-25:
So working in my KlickyNG install.

Keep having the issue that when picking up the probe to home Z, i will get and error saying:

`Error evaluating 'gcode_macro _SetProbeState:gcode': gcode.CommandError: Probe attach failed!`

And probe will still say "triggered" after picking it up.
Then, if i like twitch the probe "on/off" the mount fast for as sec, then i can have it sa "open".

- I have measured the probe, and conecctions are very stable, and not shoing any signs of bad connection, same with the mount.
- I have mounted and shimmed the mount to get a good parallel connection between magnets when the probe is mounted.

And now i also did start to test with picking up and docking the probe manualy, using commands to send it to the dock. And when doing this, i dont have any problems with it saying it's "triggered" when probe is mounted.

Any idea?

Running E3 Turbo, and connected to the Z endstop.

ArchAngel777, 2023-07-11:
Greetings, i had the same issue, sometimes it was working flawlessly and other times not at all.
My Solution: on the octopus board i had the probe voltage set to 12V, when i measured the DC voltage on the probe points i had about 11V, so the probe was not getting enough voltage and thus the probe state did not change, so set the probe voltage on the octopus board to 24V and everything was back to normal, i hope this helps someone :)

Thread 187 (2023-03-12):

Lots of inconsistencies with sensorless homing & Klicky

Print3DWorld, 2023-03-12:
Hello,

I am trying to find ways to stabilize the klicky probe with sensor less homing. Sensor less homing is not an exact science therefore it can alter the endstop position by a half mm sometimes. I have had only 2 successfully started prints since installing this klicky probe (before I had inductive stock probe), and usually it's related to probe failing to dock/pick-up or ill find the sensor attached sideways etc.

Anyway, what are some good ways to "stabilize" the klicky with sensor less homing? I will be glad to share my findings if I can tolerate them long enough, we actually use our printers to make money so I don't want to keep tinkering with this if it'll never be stable.

kyleisah, 2023-03-18:
@Print3DWorld Hey there! You are correct, sensorless homing is not an *exact* science, but is typically improved/good enough by setting a "homing" motor current so the homing is a little more consistent. You could simply go back to microswitches, or get your homing sequence nicely tuned with sensorless homing.

Print3DWorld, 2023-08-30:
> @Print3DWorld Hey there! You are correct, sensorless homing is not an _exact_ science, but is typically improved/good enough by setting a "homing" motor current so the homing is a little more consistent. You could simply go back to microswitches, or get your homing sequence nicely tuned with sensorless homing.

Hello,

I managed to tune the system quite well and finally got it to work semi-consistently with sensorless homing. I had to ensure the SGT/sensitivity is very well tuned and to get repeatable results.

60mm/s homing speed
1 amp homing current and hold current (do not set them differently, found this out the hard way!)
75 sensitivty

Closed 2023-08-30.

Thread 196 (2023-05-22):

Error message clicky macros

JanHH2019, 2023-05-22:
I have taken over the marcos for klicky in klipper without any changes and I get the error message shown in the picture
Option 'points' in section 'quad_gantry_level' must be specified

this message comes up even if i only have the klicky-probe.cfg, klicky-variables.cfg and klicky-macros.cfg. I took over all files unchanged. in none of the files can i find the section 'quad_gantry_level.

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

#Simple way to include all the various clicky macros and configurations
# the current home for this configuration is https://github.com/jlas1/Klicky-Probe, please check it
#[include ./klicky-specific.cfg] #place to put other configurations specific to your printer
[include ./klicky-variables.cfg] #Required
[include ./klicky-macros.cfg] #Required
#[include ./klicky-bed-mesh-calibrate.cfg] #bed mesh, requires klipper configuration
#[include ./klicky-screws-tilt-calculate.cfg] #help adjust bed screws automatically
#[include ./klicky-quad-gantry-level.cfg] #level 4 Z motors
#[include ./klicky-z-tilt-adjust.cfg] #level 2 or 3 Z motors

JanHH2019, 2023-05-22:
Habs found, my stupidity ...., in the Printer.cfg was commented out

Closed 2023-05-22.

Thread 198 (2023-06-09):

Homing 2nd axis (sensorless) not working correct

DerJOSh01, 2023-06-09:
Hey there,
i hope that I'm right to reach out in here.

I'm using the BTT Octopus 1.1 with BTT TMC2209 in UART with sensorless homing.

While NOT included klicky_probe my homing is working fine. Axis 1 moves to the frame, axis 2 moves to the frame. Each axis retracts a bit after contact. I attach the probe manually, home Z - everything ok.

I write axis 1 & 2 because the issue happens regardless which axis homes first.

If I include klicky it works like the following. Axis 1 moves to the frame, retracts a bit. Axis 2 moves a tiny bit in homing direction and retracts. Terminal sayes axis homed.
This happens if I select home x/y only and if I select home all.

If I manually home axis 1 and after that axis 2 everything is working fine as well. After that i can home z properly - so the position of the dock is driven to correctly, it attaches, homes, docks and moves away. All like it should.

Before, I had an SKR Mini E3 V2 with physical Endstops and there everything works fine.

So could someone help me out with this?

Kind regards JOSh

jlas1, 2023-06-11:
what are your homing scripts. i believe you need to have a dwell time between homing X and Y, that's probably why it works manually

DerJOSh01, 2023-06-11:
Hi,
Thanks for the comment, but i need again a little push.
I don't have any homing scripts except the original one, I think. The only thing I do is pressing the buttons in fluidd main screen. I don't know there or what the button leads to.
Can you help me finding this or create a homing script?

Kind regards
JOSh

jlas1, 2023-06-15:
check this guide https://docs.vorondesign.com/community/howto/clee/sensorless_xy_homing.html, should help.
Klicky supports the _home_x and _home_y macros and uses them if they are found on the configuration.

DerJOSh01, 2023-06-15:
Thanks, you got it.
I followed the instructions and it mostly works.
The thing I had to figure out is, that I for what ever reason, don't have to include homing_oderride. There my probe always showed as triggered so the klicky taught the probe is attached and homes instantly. So i went for commenting out the z option in homing_override but it didn't work. At last I don't include it ant now it's working like it should!
Thanks again and kind regards.

Closed 2023-06-15.

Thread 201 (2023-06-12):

Klicky wont attach and detach correctly. Says already attached

Cipher43, 2023-06-12:
Hello.  Im trying to setup Klicky probe on my Ender 5 plus converted to Mercury 1.1 with a stealthburner.  I changed the few variables that it says I need to but when i test with the attach probe macro it says already attached.  When i test with dock probe macro it attaches the probe.   Also if I try and run a standard homing it will perform x and y correctly and then tries to probe without picking up the klicky probe.
Thanks

jlas1, 2023-06-15:
you may have a wiring issue, then the mcu thinks that the probe is always attached.
Can you try to do query_probe with:
probe at the dock (should get triggered)
probe mounted on the toolhead (should get open)
probe mounted on the toolhead and switch pressed (should get triggered)

Cipher43, 2023-06-19:
Ok so I did the query_probe and it says open when its on the dock.

Cipher43, 2023-06-19:
Ok thanks.  I had the wires from the probe backwards.  Now when I tell it to attach it moves sideways and then says   Error evaluating 'gcode_macro _SetProbeState:gcode': gcode.CommandError: Probe attach failed!

Cipher43, 2023-06-19:
Ok so i got that first part fixed after discovering a bad spot in a wire.  Now the probe says that its triggered when docked, open when attached to the toolhead, and triggered when the button is pressed while mounted.  When I use the macro attach probe, it moves only in the y direction and picks it up and then moves back in the y direction to drop the probe.  and give this error   Error evaluating 'gcode_macro _SetProbeState:gcode': gcode.CommandError: Probe attach failed!           if I manually move it to the attach position and query the probe it states its open as if it should be connected.

For reference on this machine its an ender 5 plus converted to mercury one.1 with a stealthburner. For boards I am using a BTT skr mini e3 v2, BTT ebb sb2209, and u2c canbus on mainsail.  It wont let me post the actual printer.cfg or klickyvariables on here   so this is the best i can do.

Klickyvariables
# This macro was provided by discord user Garrettwp to whom i give my thanks for sharing it with me.
# I have tweaked it a lot.
# They are based on the great Annex magprobe dockable probe macros "#Originally developed by Mental,
# modified for better use on K-series printers by RyanG and Trails", kudos to them.
# That macro as since evolved into a klipper plugin that currently is pending inclusion in klipper,
# more information here, https://github.com/Annex-Engineering/Quickdraw_Probe/tree/main/Klipper_Macros
# User richardjm revised the macro variables and added some functions, thanks a lot
# by standing on the shoulders of giants, lets see if we can see further
#
# the current home for this version is https://github.com/jlas1/Klicky-Probe
# the 1000 values below is to give an error instead of doing something wrong, hopefully, this won't be used is a printer larger than 1 meter

[gcode_macro _User_Variables]
variable_verbose:             True    # Enable verbose output
variable_travel_speed:         400    # how fast all other travel moves will be performed when running these macros
variable_move_accel:          1000    # how fast should the toolhead accelerate when moving
variable_dock_speed:            300    # how fast should the toolhead move when docking the probe for the final movement
variable_release_speed:         300    # how fast should the toolhead move to release the hold of the magnets after docking
variable_z_drop_speed:          20    # how fast the z will lower when moving to the z location to clear the probe

variable_safe_z:         	    25    # Minimum Z for attach/dock and homing functions
# if true it will move the bed away from the nozzle when Z is not homed
variable_enable_z_hop:        True    # set this to false for beds that fall significantly under gravity (almost to Z max)

variable_max_bed_y:            355    # maximum Bed size avoids doing a probe_accuracy outside the bed
variable_max_bed_x:            355   # maximum Bed size avoids doing a probe_accuracy outside the bed

# if a separate Z endstop switch is in
# use, specify the coordinates of the switch here (Voron).
# Set to 0 to have the probe move to center of bed
variable_z_endstop_x:         0
variable_z_endstop_y:         0

#Check the documentation on klipper Dock/Undock configuration, these are dummy values
#dock location
variable_docklocation_x:      12     # X Dock position
variable_docklocation_y:      343   # Y Dock position
variable_docklocation_z:      -128    # Z dock position (-128 for a gantry/frame mount)

#Dock move, final toolhead movement to release the probe on the dock
#it's a relative move
Variable_dockmove_x:             40
Variable_dockmove_y:             0
Variable_dockmove_z:             0
#Attach move. final toolhead movement to attach the probe on the mount
#it's a relative move
Variable_attachmove_x:           0
Variable_attachmove_y:           30
Variable_attachmove_z:           0

#Umbilical to help untangle the umbilical in difficult situations
variable_umbilical:          False    # should we untabgle the umbilical
variable_umbilical_x:           15    # X umbilical position
variable_umbilical_y:           15    # Y umbilical position

# location to park the toolhead
variable_park_toolhead:      False    # Enable toolhead parking
variable_parkposition_x:       125
variable_parkposition_y:       125
variable_parkposition_z:        30

variable_version:                1    # Helps users to update the necessary variables, do not update if the variables above are not updated

#Below this remark, you normally do not need to configure
#Attach move2
Variable_attachmove2_x:          0    # intermediate toolhead movement to attach
Variable_attachmove2_y:          0    # the probe on the dock
Variable_attachmove2_z:          0    # (can be negative)

# Do not modify below
gcode:
    {% set Mx = printer['configfile'].config["stepper_x"]["position_max"]|float %}
    {% set My = printer['configfile'].config["stepper_y"]["position_max"]|float %}
    {% set Ox = printer['configfile'].config["probe"]["x_offset"]|float %}
    {% set Oy = printer['configfile'].config["probe"]["y_offset"]|float %}
    {% set Oz = printer['configfile'].config["probe"]["z_offset"]|float %}

    # If x, y coordinates are set for z endstop, assign them
    {% if z_endstop_x != 0 or z_endstop_y != 0 %}
        SET_GCODE_VARIABLE MACRO=_Probe_Variables VARIABLE=z_endstop_x VALUE={ z_endstop_x }
        SET_GCODE_VARIABLE MACRO=_Probe_Variables VARIABLE=z_endstop_y VALUE={ z_endstop_y }

    # if no x, y coordinates for z endstop, assume probe is endstop and move toolhead to center of bed
    {% else %}
        SET_GCODE_VARIABLE MACRO=_Probe_Variables VARIABLE=z_endstop_x VALUE={ (Mx * 0.5) - Ox }
        SET_GCODE_VARIABLE MACRO=_Probe_Variables VARIABLE=z_endstop_y VALUE={ (My * 0.5) - Oy }
    {% endif %}

Printer.cfg
[include klicky/klicky-probe.cfg]
[include mainsail.cfg]
#[include bigtree-tech-ebbsb-canbusv1.0.cfg]
#[include ERCF/ercf_hardware.cfg]
#[include ERCF/ercf_software.cfg]
#[include ERCF/ercf_vars.cfg]
[stepper_x]
step_pin: PB13
dir_pin: !PB12
enable_pin: !PB14
microsteps: 16
rotation_distance: 40
endstop_pin: tmc2209_stepper_x:virtual_endstop
homing_retract_dist: 0
#endstop_pin: ^PC0
position_endstop: 0
position_max: 400
homing_speed: 50

[tmc2209 stepper_x]
uart_pin: PC11
tx_pin: PC10
uart_address: 0
run_current: 0.580
stealthchop_threshold: 999999
diag_pin: ^PC0     # Set to MCU pin connected to TMC DIAG pin
driver_SGTHRS: 50  # 255 is most sensitive value, 0 is least sensitive

[stepper_y]
step_pin: PB10
dir_pin:PB2
enable_pin: !PB11
microsteps: 16
rotation_distance: 40
endstop_pin: tmc2209_stepper_y:virtual_endstop
homing_retract_dist: 0
#endstop_pin: ^PC1
position_endstop: 0
position_max: 400
homing_speed: 50

[tmc2209 stepper_y]
uart_pin: PC11
tx_pin: PC10
uart_address: 2
run_current: 0.580
stealthchop_threshold: 999999
diag_pin: ^PC1     # Set to MCU pin connected to TMC DIAG pin
driver_SGTHRS: 27 # 255 is most sensitive value, 0 is least sensitive

[stepper_z]
step_pin: PB0
dir_pin: !PC5
enable_pin: !PB1
microsteps: 16
rotation_distance: 4
endstop_pin:probe:z_virtual_endstop
#position_min: -15.0
position_max: 400
homing_speed: 12 ### Currently running my first homing speed at 20 ###
second_homing_speed: 5

[tmc2209 stepper_z]
uart_pin: PC11
tx_pin: PC10
uart_address: 1
run_current: 0.580
stealthchop_threshold: 999999

[heater_bed]
heater_pin: PC9
sensor_type: EPCOS 100K B57560G104F
sensor_pin: PC3
control: pid
pid_Kp: 54.027
pid_Ki: 0.770
pid_Kd: 948.182
min_temp: 0
max_temp: 130

[mcu]
#serial: /dev/serial/by-path/platform-3f980000.usb-usb-0:1.4:1.0
#serial: /dev/serial/by-id/usb-Klipper_Klipper_firmware_12345-if00
serial:/dev/serial/by-id/usb-Klipper_stm32f103xe_32FFDA054252303713821857-if00
      #   The serial port to connect to the MCU. If unsure (or if it
#   changes) see the "Where's my serial port?" section of the FAQ.
#   This parameter must be provided when using a serial port.
#baud: 250000
#   The baud rate to use. The default is 250000.
#canbus_uuid:ccbe1d403cf2
#   If using a device connected to a CAN bus then this sets the unique
#   chip identifier to connect to. This value must be provided when using
#   CAN bus for communication.
#canbus_interface:0483:df11
#   If using a device connected to a CAN bus then this sets the CAN
#   network interface to use. The default is 'can0'.
#restart_method:command
#   This controls the mechanism the host will use to reset the
#   micro-controller. The choices are 'arduino', 'cheetah', 'rpi_usb',
#   and 'command'. The 'arduino' method (toggle DTR) is common on
#   Arduino boards and clones. The 'cheetah' method is a special
#   method needed for some Fysetc Cheetah boards. The 'rpi_usb' method
#   is useful on Raspberry Pi boards with micro-controllers powered
#   over USB - it briefly disables power to all USB ports to
#   accomplish a micro-controller reset. The 'command' method involves
#   sending a Klipper command to the micro-controller so that it can
#   reset itself. The default is 'arduino' if the micro-controller
#   communicates over a serial port, 'command' otherwise.
[printer]
kinematics: corexy
max_velocity: 300
max_accel: 3000
max_z_velocity: 25
max_z_accel: 30

[static_digital_output usb_pullup_enable]
pins: !PA14

[bed_mesh]
speed: 120
horizontal_move_z: 10
mesh_min: 20, 24
#mesh_max: 210, 190 # Ender 5 / 5 Pro
mesh_max: 340, 310 # Ender 5 Plus
probe_count: 5,3

[board_pins]
aliases:
    # EXP1 header
    EXP1_1=PB5,  EXP1_3=PA9,   EXP1_5=PA10, EXP1_7=PB8,  EXP1_9=<GND>,
    EXP1_2=PA15, EXP1_4=<RST>, EXP1_6=PB9,  EXP1_8=PB15, EXP1_10=<5V>
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
Cipher43, 2023-07-10:
https://youtu.be/6E9X7UoHcnE
https://youtu.be/LxS_Qxsc9KY

Ok so I am still stuck on this still.  I changed out the klicky probe I was using to see if that is the issue and it wasnt.  This one is a bought one instead of made and it has a led on it to show when its attached.  I took a video of the probe doing what I can get it to do.  The first video is mounting the probe by hand and running it through the probe query.  The second is actually trying to home the machine.  When it fails I manually move the machine 30 to the side so its in docking postion and then clicking z home.  It also fails to dock after it has finished.
Thanks

Closed 2023-07-18.

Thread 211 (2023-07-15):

klipper macros homing_override does not check current z height

miker1r6, 2023-07-15:
After some confusing crashes on my voron trident I found that if you home x or y with z already homed z will move to safe_z regardless of current z position I found this when testing and my slicer end script had a g28 x in it and it just rammed the nozzle into the print.
the macro should check if the current position is greater than safe_z to decide if it is necessary to move the z.

Debug output:

10:56 am
_klicky_status_ready activating the LED STATUS_READY
10:56 am
probe: TRIGGERED
10:56 am
homing_override backing off X endstop, G0 X290.0 F12000
10:56 am
homing_override Homing X, G28 X0
10:56 am
homing_override moving toolhead to 25mm from 75.0mm in X homing seq
10:56 am
_klicky_status_homing activating the LED STATUS_HOMING
10:56 am
homing_override goint to home X
10:56 am
probe: TRIGGERED
10:56 am
moving to a safe Z distance
10:56 am
Homing X
10:56 am
G28 X

Nathan22211, 2023-07-20:
Same issue on my trident. Lost a print due to this

miker1r6, 2023-07-20:
> Same issue on my trident. Lost a print due to this

JosAr helped me solve it on the voron discord.
I believe he was going to include the fix soon but in the meantime.

You need to add this to each axis in the homing overide section of the klipper macros file.
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

jacksonliam, 2023-08-24:
This has also almost broke my printer on two occasions, after pressing cancel print and home (to get the nozzle away) it tried to first rapidly push the plastic back into the nozzle.

@miker1r6  Thanks for the patch, I was just going to comment out those Z moves when homing x/y, that's a better fix.

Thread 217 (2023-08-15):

Something in my klicky macros is creating a MCU unable to connect issue.

bcharle10, 2023-08-15:
Trying to get Klicky installed and working, but have run into an issue that has had me stuck and scratching my head for several days and I am not sure what to try next.  Not sure if I have a setting wrong that I am unaware of?  Some weird conflict with my hardware?

I have a working Mercury one printer with SKR Mini e3 V2.0 board until I imported the Klicky macros.  Klicky Variables, Macros, Probe, bed mesh calibrate.  After several different USB cables and a complete delete and re-install of Klipper, Moonraker, Mainsail, and reflashing the printer, the printer works again but ONLY if I comment out [include klicky_probe.cfg] or [include klicky_macros.cfg] inside klicky_probe.cfg.

[include klicky_macros] = MCU unable to connect error -> Klippy (7).log
#[include klicky_macros] = working printer -> Klippy (6).log

Any suggestions?

[klippy (7).log](https://github.com/jlas1/Klicky-Probe/files/12353646/klippy.7.log)
[klippy (6).log](https://github.com/jlas1/Klicky-Probe/files/12353647/klippy.6.log)

bcharle10, 2023-08-16:
Thanks for the quick respond.  I am not quite sure what you mean by check if I have /dev/serial/by-id/usb-Klipper_stm32f103xe_34FFD8054D42373923560243-if00.  It is there when I check in kiauh, and also when I run "ls /dev/serial/by-id/ *".

So I tried a few more things last night, and realized that if I start up mainsail with the printer powered on then power cycle my printer (manually power off then on), klipper connects automatically and works fine.  But connecting at mainsail startup, Restart, and Firmware_Restart options do not work like they used to.  It just seems strange that the klicky macros trigger this odd behavior.  Is there a size limit for klipper config files that could be messing with the connection?  Are some setups not able to process nested config files?

At least I am back up and printing, and working on finishing my klicky setup.

bcharle10, 2023-09-08:
There must be something in the Linux MX laptop that I am using that was causing this strange behavior.  I picked up a raspberry pi 2 and after getting it set up, I have had none of the original firmware restarting issues.  Klicky macros are now working as they should.

Closed 2023-09-08.

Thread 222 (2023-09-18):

Klicky causing Y to not home

Collapsednut, 2023-09-18:
If I issue G28 the X axis will home but not the Y and then it attempts a probe attach. If I issue G28 Y it will home Y. It's as though the Y axis is being skipped for homing with G28.

[klippy (13).log](https://github.com/jlas1/Klicky-Probe/files/12644008/klippy.13.log)
[printer.txt](https://github.com/jlas1/Klicky-Probe/files/12644024/printer.txt)
[klicky-variables.txt](https://github.com/jlas1/Klicky-Probe/files/12644025/klicky-variables.txt)

Collapsednut, 2023-09-18:
Resolved by using sensorless homing .cfg by #181

pasha4ur, 2023-09-25:
Hello

Where did you download "klicky-sensorless-homing.cfg"? I can't find it and have same problem (

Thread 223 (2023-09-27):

Voron V0 Fan can not be installed Skeeter_Cowling_wKlicky_.stl

freakezoid1604, 2023-09-27:
Hello
I print the following housing for the Mosquito hotend :

[Printers/Voron/v0/v0_STL/Skeeter_Cowling_wKlicky_.stl](https://github.com/jlas1/Klicky-Probe/blob/main/Printers/Voron/v0/v0_STL/Skeeter_Cowling_wKlicky_.stl)

I was not able to install the fan. The body is not flat in the fan area and the indentation is missing.
Maybe I got the wrong STL.
Please help thanks
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

freakezoid1604, 2023-09-27:
It should like that
Found here -> [https://www.printables.com/de/model/113212-voron-0-mini-afterburner-30mm-fan-for-mosquito#preview:file-L9DlX](url)
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

freakezoid1604, 2023-09-29:
Ok I use the wrong fan. Issue can be closed.

Closed 2023-09-29.

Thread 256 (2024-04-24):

Klipper Macros and Sensorless Homing

seanmccully, 2024-04-24:
There is something about these MACROS that cause Sensorless Homing to consistently fail. It is always on the second AXIS.

 If Y is first than X will not HOME.
If  X is first than Y will not HOME.

Especially with the TMC5160 drivers (at least on my printer) Sensorless Homing can be a bit finicky. But there is something in these MACROS, that feels like possibly a bug in Klipper. Doing a single axis homing for both X,Y than a G28 for all three axis(s) the second axis will still consistently fail.

The above routine, at least on my printer will always clear any stickiness with sensorless homing on the TMC5160(s).

elSaxoo, 2024-04-30:
Hey, i had the same problem. For me using my own _HOME_X and _HOME_Y macros solved it for me.

> XY Sensorless homing
If you are using sensorless homing, and have your own X and/or Y homing macros, you can use override the klicky macros behavior with your very own _HOME_X and _HOME_Y macros.
If they exist on your klipper configuration, klicky macro will use them instead of the default G28 commands.

I put the following into the printer.cfg and it works perfectly.

```
[gcode_macro _HOME_X]
gcode:
    # Always use consistent run_current on A/B steppers during sensorless homing
    {% set RUN_CURRENT_X = printer.configfile.settings['tmc2209 stepper_x'].run_current|float %}
    {% set RUN_CURRENT_Y = printer.configfile.settings['tmc2209 stepper_y'].run_current|float %}
    {% set HOME_CURRENT = 0.7 %}
    SET_TMC_CURRENT STEPPER=stepper_x CURRENT={HOME_CURRENT}
    SET_TMC_CURRENT STEPPER=stepper_y CURRENT={HOME_CURRENT}

    # Home
    G28 X
    # Move away
    G91
    G1 X10 F1200

    # Wait just a second… (give StallGuard registers time to clear)
    G4 P1000
    # Set current during print
    SET_TMC_CURRENT STEPPER=stepper_x CURRENT={RUN_CURRENT_X}
    SET_TMC_CURRENT STEPPER=stepper_y CURRENT={RUN_CURRENT_Y}

[gcode_macro _HOME_Y]
gcode:
    # Set current for sensorless homing
    {% set RUN_CURRENT_X = printer.configfile.settings['tmc2209 stepper_x'].run_current|float %}
    {% set RUN_CURRENT_Y = printer.configfile.settings['tmc2209 stepper_y'].run_current|float %}
    {% set HOME_CURRENT = 0.7 %}
    SET_TMC_CURRENT STEPPER=stepper_x CURRENT={HOME_CURRENT}
    SET_TMC_CURRENT STEPPER=stepper_y CURRENT={HOME_CURRENT}

    # Home
    G28 Y
    # Move away
    G91
    G1 Y10 F1200

    # Wait just a second… (give StallGuard registers time to clear)
    G4 P1000
    # Set current during print
    SET_TMC_CURRENT STEPPER=stepper_x CURRENT={RUN_CURRENT_X}
    SET_TMC_CURRENT STEPPER=stepper_y CURRENT={RUN_CURRENT_Y}

seanmccully, 2024-04-30:
I used those homing macros for a long time, and they just don't work consistently for me. In my current setup (48v, TMC5160, LDO2804AH)  I have found mostly by accident that the most consistent setting was not having any homing overrides.

Setting the timers, changing the current just appears to add noise and inconsistencies in the results. Letting Klipper just do the sensorless homing appears to work 99.9% of the time.

I need to investigate more into why,  Increasing SGT is not the answer, because while sometimes it will clear a motor not homing, other times it will be too high and skip steps.

janderholm, 2025-04-05:
I also had problems with the above macros. These work well for me:

```
[gcode_macro _HOME_X]
gcode:
    G28 X
    G90
    G0 X320 F6000
    M400 ;

[gcode_macro _HOME_Y]
gcode:
    G28 Y
    G90
    G0 Y320 F6000
    M400
```

A guess is that the M400 is important to let everything run to a halt wheres the 1 second wait is just guesswork.

Be mindful of the 320 position in the macros. That's just a position that works well with my dock placement.

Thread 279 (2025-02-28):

dock_on_zhome state confusion

bombela, 2025-02-28:
If  `dock_on_zhome` is true (the default), the probe is docked before Z home but not after.
If false, this reverses. The probe is not docked before Z home, but is docked after.

In other words, it is impossible to Z home without the probe being docked at some point.

This strikes me as a bug in the logic. This should either be two config variables and/or a dynamic parameter for optionally docking post Z homing.

Because in the current state, one cannot optimize a sequence of home XYZ, QGL, auto-z-cal, without the probe being docked and re-attached multiple times. I have hacked the macros quick and dirty for my application, and I figured I should bring this to your attention.

https://github.com/jlas1/Klicky-Probe/blob/ab86f91d47ac7353a0a7c7e0de26542dca00f63e/Klipper_macros/klicky-macros.cfg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

Koza666, 2025-03-09:
Faced the similar issue with slighty different setup (triple z printer and z-tilt routine). For me the workaround was to home X and Y axis separetly and add proble lock before homing Z, to avoid docking probe multiple times. My start print macro looks something like this:

```
[gcode_macro START_PRINT]
gcode:
    {% set BED_TEMP = params.BED_TEMP|default(60)|float %}
    {% set EXTRUDER_TEMP = params.EXTRUDER_TEMP|default(190)|float %}
    # Start bed heating
    M190 S{BED_TEMP}
    BED_MESH_CLEAR

    # Use absolute coordinates
    G90

    # Reset the G-Code Z offset
    SET_GCODE_OFFSET Z=0.0

    # Home the printer
    G28 X Y
    Attach_Probe_Lock
    G28 Z
    Z_TILT_ADJUST
    BED_MESH_CALIBRATE
    Dock_Probe_Unlock
    Smart_Park
    M109 S{EXTRUDER_TEMP}
    LINE_PURGE

```

jlas1, 2025-04-06:
@bombela is the correct solution in the current state of klicky macros

bombela, 2025-04-06:
I am not sure to understand the question.

Do you mean you have pushed some changes and want me to take a look?

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

jlas1, 2025-04-07:
sorry for not being clearer, what i wanted to say, is that this approach is the best one to minimize probe docking and attaching:
    # Home the printer
    G28 X Y
    Attach_Probe_Lock
    G28 Z
    Z_TILT_ADJUST or QGL
    BED_MESH_CALIBRATE
    Dock_Probe_Unlock

Closed 2025-04-06.

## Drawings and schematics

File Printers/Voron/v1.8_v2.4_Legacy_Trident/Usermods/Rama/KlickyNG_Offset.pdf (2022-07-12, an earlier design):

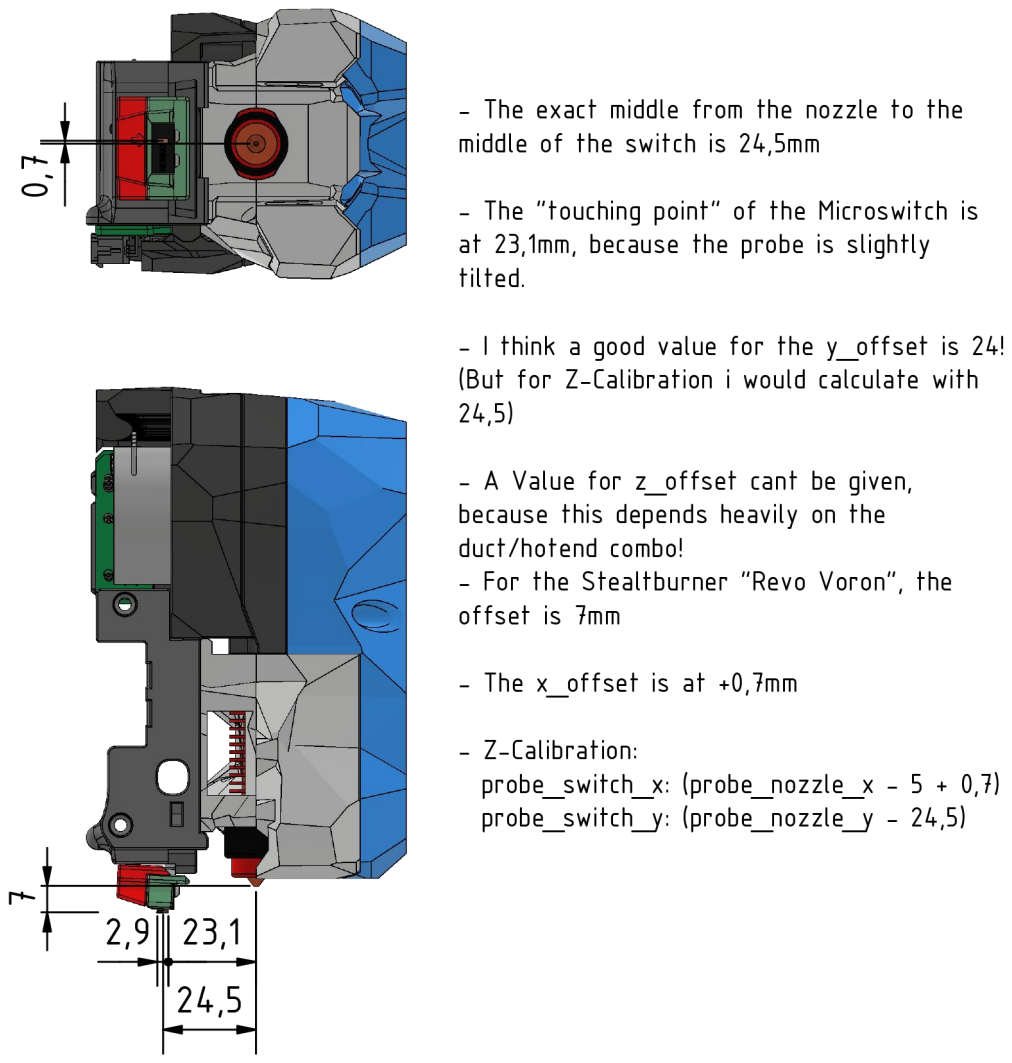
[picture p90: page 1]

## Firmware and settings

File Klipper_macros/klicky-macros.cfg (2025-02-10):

# This macro was provided by discord user Garrettwp to whom i give my thanks for sharing it with me.
# I have tweaked it a lot.
# They are based on the great Annex magprobe dockable probe macros "#Originally developed by Mental,
# modified for better use on K-series printers by RyanG and Trails", kudos to them.
# That macro as since evolved into a klipper plugin that currently is pending inclusion in klipper,
# more information here, https://github.com/Annex-Engineering/Quickdraw_Probe/tree/main/Klipper_Macros
# User richardjm revised the macro variables and added some functions
# User sporkus added led status notifications
# Thanks to all who helped,
# by standing on the shoulders of giants, lets see if we can see further
#
# the current home for this version is https://github.com/jlas1/Klicky-Probe

[respond]

[gcode_macro _Probe_Variables]
variable_probe_attached:            False
variable_probe_state:               False
variable_probe_lock:                False
variable_probe_z_homed:             False
variable_z_endstop_x:               0
variable_z_endstop_y:               0
gcode:


#checks if the variable definitions are up to date
[gcode_macro _klicky_check_variables_version]
gcode:
    {% set version = printer["gcode_macro _User_Variables"].version|default(0) %}

    {% if version != 1 %}
        { action_raise_error("Please update your klicky variables, there are some functionality changes") }
    {% endif %}

[gcode_macro _KlickyDebug]
gcode:
    {% set message  = params.MSG %}
    {% set debug = printer["gcode_macro _User_Variables"].debug|default(False) %}

    {% if debug %}
        { action_respond_info(message) }
    {% endif %}


[gcode_macro _exit_point]
gcode:
    {% set function  = 'pre_' ~ params.FUNCTION %}
    {% set move  = params.MOVE|default(0) %}
    {% set speed = printer["gcode_macro _User_Variables"].travel_speed %}

    # mandatory to save the new safe position
    M400
    SET_VELOCITY_LIMIT ACCEL={printer.configfile.settings.printer.max_accel}
    RESTORE_GCODE_STATE NAME={function} MOVE={move} MOVE_SPEED={speed}


[gcode_macro _entry_point]
gcode:
    {% set function  = 'pre_' ~ params.FUNCTION %}
    {% set move_accel = printer["gcode_macro _User_Variables"].move_accel|default(1000) %}
    # mandatory to save the new safe position
    M400
    SAVE_GCODE_STATE NAME={function}
    # removes the Z offset for better bed based docking
    SET_GCODE_OFFSET Z=0
    # all the macros initially assume absolute positioning
    G90
    # set a safe(sane) Acceleration
    SET_VELOCITY_LIMIT ACCEL={move_accel}

[gcode_macro _Homing_Variables]
gcode:
    {% set reset  = params.RESET|default(0) %}
    {% if reset %}
        SET_GCODE_VARIABLE MACRO=_Probe_Variables VARIABLE=probe_lock VALUE={ False }
    {% endif %}

##########################
# Attach probe and lock it
[gcode_macro Attach_Probe_Lock]
description: Attaches Klicky Probe, can only be docked after unlocking
gcode:
    Attach_Probe
    _Probe_Lock

########################
# Dock probe and lock it
[gcode_macro Dock_Probe_Unlock]
description: Docks Klicky Probe even if it was locked
gcode:
    _Probe_Unlock
    Dock_Probe

##############
# Unlock Probe
[gcode_macro _Probe_Unlock]
description: Unlocks Klicky Probe state
gcode:
    _KlickyDebug msg="_Probe_Lock setting probe_lock variable to False"
    SET_GCODE_VARIABLE MACRO=_Probe_Variables VARIABLE=probe_lock VALUE={ False }

############
# Lock Probe
[gcode_macro _Probe_Lock]
description: Locks Klicky Probe state
gcode:
    _KlickyDebug msg="_Probe_Lock setting probe_lock variable to True"
    SET_GCODE_VARIABLE MACRO=_Probe_Variables VARIABLE=probe_lock VALUE={ True }

###################
# Klicky Dock Servo Deploy

[gcode_macro _DeployKlickyDock]
description: Deploys Klicky servo-controlled dock
gcode:
    {% set enable_dock_servo = printer["gcode_macro _User_Variables"].enable_dock_servo|default(False) %}
    {% set servo_delay = printer["gcode_macro _User_Variables"].servo_delay|default(1000)|int %}
    {% set servo_name = printer["gcode_macro _User_Variables"].servo_name %}
    {% set servo_deploy = printer["gcode_macro _User_Variables"].servo_deploy|default(360)|float %}

    #wait for all the moves to complete
    M400
    {% if enable_dock_servo != False %}
        _KlickyDebug msg="_DeployKlickyDock Klicky servo configuration enabled"
        {% if servo_deploy == 360 %}
            { action_raise_error("Klicky: servo active on klicky-variables, but no servo deploy angle specified") }
        {% endif %}
        _KlickyDebug msg="_DeployKlickyDock SET_SERVO SERVO={servo_name|string} ANGLE={servo_deploy}"
        SET_SERVO SERVO={servo_name|string} ANGLE={servo_deploy}
        M400
        G4 P{servo_delay}
        _KlickyDebug msg="_DeployKlickyDock SET_SERVO SERVO={servo_name|string} WIDTH=0"
        SET_SERVO SERVO={servo_name|string} WIDTH=0
    {% elif printer["gcode_macro _DeployDock"] is defined %}
        _KlickyDebug msg="_DeployKlickyDock calling _DeployDock"
        _DeployDock
    {% endif %}

####################
# Dock Servo Retract

[gcode_macro _RetractKlickyDock]
description: Retracts Klicky servo-controlled dock
gcode:
    {% set enable_dock_servo = printer["gcode_macro _User_Variables"].enable_dock_servo|default(False) %}
    {% set servo_delay = printer["gcode_macro _User_Variables"].servo_delay|default(1000)|int %}
    {% set servo_name = printer["gcode_macro _User_Variables"].servo_name %}
    {% set servo_retract = printer["gcode_macro _User_Variables"].servo_retract|default(360)|float %}

    #wait for all the moves to complete
    M400
    {% if enable_dock_servo != False %}
        _KlickyDebug msg="_RetractKlickyDock Klicky servo configuration enabled"
        {% if servo_retract == 360 %}
            { action_raise_error("Klicky: servo active on klicky-variables, but no servo retract angle specified") }
        {% endif %}
        _KlickyDebug msg="_RetractKlickyDock SET_SERVO SERVO={servo_name|string} ANGLE={servo_retract}"
        SET_SERVO SERVO={servo_name|string} ANGLE={servo_retract}
        M400
        G4 P{servo_delay}
        _KlickyDebug msg="_RetractKlickyDock SET_SERVO SERVO={servo_name|string} WIDTH=0"
        SET_SERVO SERVO={servo_name|string} WIDTH=0
    {% elif printer["gcode_macro _RetractDock"] is defined %}
        _KlickyDebug msg="_RetractKlickyDock calling _RetractDock"
        _RetractDock
    {% endif %}
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

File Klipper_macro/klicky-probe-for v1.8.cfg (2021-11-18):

# This macro was provided by discord user Garrettwp to whom i give my thanks for sharing it with me.
# I have tweaked it a lot.
#
# this macro is  based on the great Annex magprobe dockable probe macros "#Originally developed by Mental, modified for better use on K-series printers by RyanG and Trails"
# that macro can be found here https://github.com/Annex-Engineering/Annex-Engineering_Other_Printer_Mods/blob/master/All_Printers/Microswitch_Probe/Klipper_Macros/dockable_probe_macros.cfg
#
# by standing on the shoulders of giants, lets see if we can see further

[gcode_macro _User_Variables]
variable_verbose:               True  # Enable verbose output
variable_travel_speed:          200   # how fast all other travel moves will be performed when running these macros
variable_dock_speed:            50    # how fast should the toolhead move when docking the probe for the final movement
variable_release_speed:         75    # how fast should the toolhead move to release the hold of the magnets after docking
variable_z_drop_speed:          20    # how fast the z will lower when moving to the z location to clear the probe
variable_home_z_height:         10    # Z when homing

#bed type
variable_gravity:             'bed'   # What goes down with gravity, bed or gantry?
variable_max_bed_y:             250   # maximum Bed size avoids doing a probe_accuracy outside the bed

# if a separate Z endstop switch is in
# use, specify the coordinates of the switch here (Voron).
# Set to 0 to have the probe move to center of bed
variable_z_endstop_x:            1000
variable_z_endstop_y:            1000

#dock location 
variable_docklocation_x:        1000  # X Dock position
variable_docklocation_y:        1000  # Y Dock position
variable_docklocation_z:        -128  # Z dock position (-128 for a gantry mount)
variable_dockarmslenght:        30    # Dock arms lenght, toolhead movement necessary to clear the dock arms

#Umbilical to help untangle the umbilical in difficult situations
variable_umbilical:             False # should we untabgle the umbilical
variable_umbilical_x:           15    # X umbilical position
variable_umbilical_y:           15    # Y umbilical position

# location to park the toolhead
variable_park_toolhead:         False  # Enable toolhead parking
variable_parkposition_x:        75
variable_parkposition_y:        75
variable_parkposition_z:        30

# Do not modify below
gcode:
    {% set Mx = printer['configfile'].config["stepper_x"]["position_max"]|float %}
    {% set My = printer['configfile'].config["stepper_y"]["position_max"]|float %}
    {% set Ox = printer['configfile'].config["probe"]["x_offset"]|float %}
    {% set Oy = printer['configfile'].config["probe"]["y_offset"]|float %}
    {% set Oz = printer['configfile'].config["probe"]["z_offset"]|float %}

    # if docklocation_z is zero, use Home Z height for safety
    {% if docklocation_z == 0 %}
        SET_GCODE_VARIABLE MACRO=_Probe_Variables VARIABLE=docklocation_z VALUE={ home_z_height }
    {% endif %}

    # If x, y coordinates are set for z endstop, assign them
    {% if z_endstop_x != 0 or z_endstop_y != 0 %}
        SET_GCODE_VARIABLE MACRO=_Probe_Variables VARIABLE=z_endstop_x VALUE={ z_endstop_x }
        SET_GCODE_VARIABLE MACRO=_Probe_Variables VARIABLE=z_endstop_y VALUE={ z_endstop_y }

    # if no x, y coordinates for z endstop, assume probe is endstop and move toolhead to center of bed
    {% else %}
        SET_GCODE_VARIABLE MACRO=_Probe_Variables VARIABLE=z_endstop_x VALUE={ (Mx * 0.5) - Ox }
        SET_GCODE_VARIABLE MACRO=_Probe_Variables VARIABLE=z_endstop_y VALUE={ (My * 0.5) - Oy }
    {% endif %}
# This macro was provided by discord user Garrettwp to whom i give my thanks for sharing it with me.
# I have tweaked it a lot.
#
# this macro is  based on the great Annex magprobe dockable probe macros "#Originally developed by Mental, modified for better use on K-series printers by RyanG and Trails"
# that macro can be found here https://github.com/Annex-Engineering/Annex-Engineering_Other_Printer_Mods/blob/master/All_Printers/Microswitch_Probe/Klipper_Macros/dockable_probe_macros.cfg
#
# by standing on the shoulders of giants, lets see if we can see further

[gcode_macro _Probe_Variables]
variable_probe_attached:            False
variable_probe_state:               False
variable_probe_lock:                False
variable_z_endstop_x:               0
variable_z_endstop_y:               0
gcode:


[gcode_macro _exit_point]
gcode:
    {% set function  = 'pre_' ~ params.FUNCTION  %}
    {% set move  = params.MOVE|default(0)  %}
    # mandatory to save the new safe position
    M400
    RESTORE_GCODE_STATE NAME={function} MOVE={move}


[gcode_macro _entry_point]
gcode:
    {% set function  = 'pre_' ~ params.FUNCTION  %}
    # mandatory to save the new safe position
    M400
    SAVE_GCODE_STATE NAME={function}
    # removes the Z offset for better bed based docking
    SET_GCODE_OFFSET Z=0
    # all the macros initially assume absolute positioning
    G90

[gcode_macro _Homing_Variables]
gcode:
    {% set R  = params.RESET|default(0)  %}
    {% if R %}
        SET_GCODE_VARIABLE MACRO=_Probe_Variables VARIABLE=probe_lock VALUE={ False }
    {% endif %}

# Attach probe and lock it
[gcode_macro Attach_Probe_Lock]
description: Attaches Klicky Probe, can only be docked after unlocking
gcode:
    Attach_Probe
    SET_GCODE_VARIABLE MACRO=_Probe_Variables VARIABLE=probe_lock VALUE={ True }

# Dock probe and lock it
[gcode_macro Dock_Probe_Unlock]
description: Docks Klicky Probe even if it was locked
gcode:
    SET_GCODE_VARIABLE MACRO=_Probe_Variables VARIABLE=probe_lock VALUE={ False }
    Dock_Probe

# Unlock Probe
[gcode_macro Probe_Unlock]
description: Unlocks Klicky Probe state
gcode:
    SET_GCODE_VARIABLE MACRO=_Probe_Variables VARIABLE=probe_lock VALUE={ False }

# Lock Probe
[gcode_macro Probe_Lock]
description: Locks Klicky Probe state
gcode:
    SET_GCODE_VARIABLE MACRO=_Probe_Variables VARIABLE=probe_lock VALUE={ True }
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

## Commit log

2021-05-12 Initial upload
    first upload, STL files with correct orientation, CAD file, photos and Klipper macro file
    [KlickyProbe AB mount.stl, KlickyProbe Dock Mount Fixed.stl, KlickyProbe Dock Mount Variable pt1.stl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]
2021-05-12 corrected BOM tables added contact
2021-05-12 Image descriptions improved, macro bug solved
    Should have solved a bug on the macro where the Z weight was not correct when docking.
    Images renamed and resized
    Readme with a new front image
    [klicky-probe.cfg]
2021-05-13 Macro update
    Solved the bug that after a QGL the Z was offset and required a new G28
    Improved the probe dock and undock with a better configured arm distance and a possibility to change Z when docking and undocking (bed mounted dock)
    [klicky-probe.cfg]
2021-05-14 added the missing attribution
    Added references and thanks to Annex project, Euclid Project, Garrettwp, Mental, RyanG and Trail
    [klicky-probe.cfg]
2021-05-15 Update klicky-probe.cfg
    simplifies the code, uses more inbuilt functions, it is no more necessary to remove the [homing_override] from printer.cfg if using the physical Z endstop
    [klicky-probe.cfg]
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2021-05-17 Update klicky-probe.cfg
    Corrected a bug that prevented docking on a Z endstop
    [klicky-probe.cfg]
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2021-05-21 Updated CAD, STL and macro
    Update the parts for:
    Better fit for the self tapping screws on the microswitch
    Better pressfit for the switch and magnets
    Added a dock grantry save and restore Z offset when docking,to allow the dock to work better with auto Z calibration
    [KlickyProbe AB mount.stl, KlickyProbe Dock Mount Fixed.stl, KlickyProbe Dock Mount Variable pt1.stl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]
2021-05-21 corrected pull up Z on G28
    [klicky-probe.cfg]
2021-05-24 Move the nozzle to correct location when doing a probe_calibrate or probe_accuracy
    [klicky-probe.cfg]
2021-05-24 Added safety for probe_calibrate and probe_accuracy to avoid crashing the bed
    [klicky-probe.cfg]
2021-05-25 revised dock and probe
    Dock and probe revised to improve the docking fit
    [KlickyProbe Probe Dock v0_1.stl, KlickyProbe Probe Dock v0_2.stl, KlickyProbe Probe v0_1.stl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]
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2021-05-25 Update KlickyProbe Probe v0_2.stl
    corrected some chanfers on probe stl
    [KlickyProbe Probe v0_2.stl]
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2021-05-27 Corrected some 1.8 macro typos
    [klicky-probe-for v1.8.cfg]
2021-05-28 Update klicky-probe.cfg
    makes sure that after attaching the probe the toolhead is at a safe Z distance
    [klicky-probe.cfg]
2021-05-30 Correct positioning of the magnets
    Polarity reversal through decaying alternating magnetic field for the distribution of the magnetic domain magnetization direction will result in a demagnetization of the magnets.
    Friction will accelerate this process.
    To prevent this issue, the three magnets must be installed with the same polarity thus creating a single coherent magnetic domain.
    Tested in production, works well on multiple printers.
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2021-06-01 Fix syntax in parameter loop
    Fix the loop to separate the parameter in the loop, just adding a space in the formatting string
    [klicky-probe-for v1.8.cfg, klicky-probe.cfg]
2021-06-01 added new probe dock mount
    added a new probe dock mount to allow a purge/scrub bucket on the left side of the bed.
    [KlickyProbe Dock Side Mount Fixed pt1.stl, KlickyProbe Dock Side Mount Fixed pt2.stl, KlickyProbe Probe Dock v0_2.stl]
2021-06-01 Update README.md
    added the fixed sidemount dock mount
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2021-06-14 Updated files
    Updated STL files:
    4mm smaller Gantry dock (no loss of Y travel)
    Voron Logo added (thanks to oc_geek)
    Small probe update (thanks to oc_geek)
    [KlickyProbe AB mount.stl, KlickyProbe Dock Mount Fixed.stl, KlickyProbe Dock Mount Variable pt1.stl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]
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2021-07-07 Add udpated fixed docs for use with the MGN12 x carriage mod.
    [probe_dock_mount_fixed.stl, probe_dock_side_mount_fixed.stl]
2021-07-07 Fix part orientation and remove microswitch from right carriage STL.
    [probe_dock_mount_fixed.stl, probe_dock_side_mount_fixed.stl, x_carriage_frame_mgn12_left.stl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]
2021-07-07 Add microswitch to carriage CAD to validate clearances.
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2021-07-12 Rename V2.4 X carriage mod STLs so it's clear what they're for.
    [v2.4_x_carriage_dock_mount_fixed.stl, v2.4_x_carriage_dock_side_mount_fixed.stl]
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2021-07-26 V2.4 MGN12: Improve magnet tolerances for a more positive fit.
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2021-08-09 Create README.md
    corrected the path of some images
    Changed the SKR wiring text, to better reflect on the necessary connections
2021-08-16 moved CAD with additional holes to usermods
    moved CAD with additional holes to usermods
    [KlickyProbe_v0_2_additional holes for wire.step]
2021-08-17 File organization
    Removed some spaces and corrected some spelling mistakes
    [KlickyProbe AB mount.stl, KlickyProbe Probe Dock v0_1.stl, KlickyProbe Probe v0_1.stl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]
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2021-08-25 V2.4 MGN12: Fix hall effect magnet location.
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2021-08-28 corrected PROBE_ACCURACY macro
    corrected some gcode saves
    [klicky-probe.cfg]
2021-08-29 Update klicky-probe-for v1.8.cfg
    corrected endif macro error
    [klicky-probe-for v1.8.cfg]
2021-09-06 new gcode macro capabilities
    updated the configuration to use the new gcode macro capabilities
    [z_calibration.cfg]
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2021-09-25 Corrected the Righ sidemount part
    [KlickyProbe_Dock_Side_Mount_Fixed_RightArm.stl, KlickyProbe_v0_2.step]
2021-09-26 added G90 on G28Z
    It seems that Octoprint adds a G91 before doing a G28 Z, messing with the toolhead move
    [klicky-probe-for v1.8.cfg, klicky-probe.cfg]
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2021-10-04 Update README.md
    added a probe_accuracy warning, to avoid head craches
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2021-10-11 revised klick-probe.cfg
    added better macro descriptions, internal functions are now hidden and probe accuracy will not be performed outside the bed on the Y
    [klicky-probe.cfg]
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2021-10-22 press fit helper
    Added a press fit helper to help when using a vive or a hard surface when installing the magnets
    [AB_mount_press_Helper.stl, KlickyProbe_v0_2.step, KlickyProbe_v0_2_20.step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]
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2021-11-01 Update README.md
    Corrected typo on probe definition
2021-11-14 add missing G90 to _Home_Z
    [klicky-probe.cfg]
2021-11-15 added save and restore Gcodes
    Now the macros set the correct Absolute mode for toolhead movement and restore the previous configuration on exit
    [klicky-probe.cfg]
2021-11-15 corrected bed option
    corrected the default for the gravity variable for a v2
    [klicky-probe.cfg]
2021-11-15 completed the gravity variable correction
    [klicky-probe.cfg]
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2021-11-16 corrected some G28 issues
    [klicky-probe-for v1.8.cfg]
2021-11-16 corrected Y docking detection on G28
    [klicky-probe-for v1.8.cfg]
2021-11-16 Corrected some G28 bugs, small updates
    [klicky-probe.cfg]
2021-11-16 corrected duplicated functions
    [klicky-probe.cfg]
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2021-11-23 New VT config file v1.8 file corrected
    also small update on the klicky probe
    [AB_mount_magnet_holder.stl, AB_mount_magnet_press.stl, AB_mount_press_Helper.stl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]
2021-12-14 corrected Zhop behavior
    Clarified and enabled Z hop behavior for safer operation of large beds that do not move parallel to the gantry when powered off
    [klicky-probe-for_VT.cfg, klicky-probe-for_v1.8.cfg, klicky-probe.cfg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]
2021-12-14 update with missing variables
    [klicky-probe-for_Trident.cfg, klicky-probe-for_v1.8.cfg, klicky-probe.cfg]
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2021-12-22 Voron Trident Dock
    The 2.4 Dock and Variable Dock take up quite a lot of space which could be better used for nozzle scrubbing etc.
    I've created an alternative Dock, that attaches to the rear left vertical profile.
    [KlickyProbe_Dock_Mount_Trident.stl, KlickyProbe_v0_2_20.step]
2021-12-30 fix picture in STL/README.md
2021-12-31 Replace ACTION with params.ACTION in _CheckProbe
    [klicky-probe.cfg]
2021-12-31 Convert { ACTION } to { params.ACTION } for Trident and v1.8
    [klicky-probe-for_Trident.cfg, klicky-probe-for_v1.8.cfg]
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2022-01-09 correct names
    [ender_5_plus-arm_v.1-body.step, ender_5_plus-arm_v.1-body.stl, ender_5_plus-arm_v.1.FCStd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]
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2022-01-12 corrected v0 STL's warnings
    [DockMount_variable.stl, Front_cowling_mount.stl, klicky-z-calibration.cfg]
2022-01-12 corrected v0 Y stepper reference
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2022-01-24 chore(docs): fix voron klipper config setup notes
2022-01-26 First commit of Dock mount fixed S user mod
    [Dock_mount_fixed_S.step, Dock_mount_fixed_S.stl]
2022-01-30 Update README.md
    Fixed case issue with klicky-probe.cfg file line. Now all lower case as per file naming in repository.
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2022-02-11 V2 Fixed dock correction
    was 2mm short
    [Dock_mount_fixed_v2.stl]
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2022-02-21 reworked README and file organization
    [Dock_mount_Ender5.step, KlickyProbe_AB_mount_v2.stl, Mount_magnet_holder.stl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]
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2022-02-21 directory locations corrections
    [KlickyProbe_AB_mount_v2.stl, Mount_magnet_holder.stl, Mount_magnet_pressfit_helper.stl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]
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2022-03-01 corrected Mosquito integrated cowlings
    [Sherpa_Mini_Mosquito_Cowling_wKlicky.stl, Skeeter_Cowling_wKlicky.stl, Skeeter_Cowling_wKlicky_.stl]
2022-03-11 Update README.md
    Fix error where it stated long probe was used when it should be the standard one.
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2022-03-24 small macro updates
    to complete the pre and post macro setup
    to include MercuryOne on the documentation
    [klicky-macros.cfg]
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2022-03-26 corrected dock orientation
    [Probe_Dock_v2.1.stl]
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2022-03-29 fix filename typo
    [[a]_klicky_dock_x1.stl]
2022-03-29 moved to the final location
    Added better description
    Added KlickSwipe mod to V0 usermods
    [KlickSwipe.f3d, KlickSwipe.step, [a]_klicky_dock_bottom_x1.stl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]
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2022-04-25 corrected wire cable distance
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2022-05-07 Add check for _HOME_Y to all instances of Y homing
    The early y_homing for y oriented docks was not using _HOME_Y if available.
    [klicky-macros.cfg]
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2022-05-11 CAD and STL added, photos path correction
    [2mm_NG_extender.stl, KlickyNG v3.28.step, KlickyNGProbe_v3_Body.stl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]
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2022-05-13 status led conflict fix
    [klicky-bed-mesh-calibrate.cfg]
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2022-05-16 Update klicky-servo-dock.cfg
    updated for correct variables and macro definitions
    [klicky-servo-dock.cfg]
2022-05-16 Update klicky-probe.cfg
    updated to add klicky-servo-dock.cfg and fix spelling
    [klicky-probe.cfg]
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2022-05-16 Update klicky-servo-dock.cfg
    missing credit, and other changes
    [klicky-servo-dock.cfg]
2022-05-16 updated Zip files, small fixes
    removed dockmove and attatchmove zero verification, as the code has a version check now.
    added M400 before the servo dock moves
    [klicky-macros.cfg]
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2022-05-17 corrected Sherpa VoronRevo cowling
    [Serpa_VoronRevo_Cowling_wKlicky.3mf, Sherpa_VoronRevo_Cowling_wKlicky.stl]
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2022-05-18 Update klicky-variables.cfg
    added 'enable' to variable name for easier understanding across files, fixed typo :P
    [klicky-variables.cfg]
2022-05-18 Update klicky-macros.cfg
    added _RetractDock and _DeployDock Macros with extended variable configuration. Klipper will check if enable_dock_servo is true or false, and respond by using the macros accordingly.
    [klicky-macros.cfg]
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2022-05-18 Update klicky-macros.cfg
    made macros more conditional on servo configuration being defined as True
    [klicky-macros.cfg]
2022-05-18 use internal macro names to avoid clutter
    [klicky-bed-mesh-calibrate.cfg, klicky-macros.cfg, klicky-quad-gantry-level.cfg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]
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2022-05-20 Update klicky-macros.cfg
    Added a `WIDTH=0` call to kill the servo after _RetractDock
    [klicky-macros.cfg]
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2022-05-21 Update klicky-macros.cfg
    still enables a simple overide of klicky macros servo dock
    safer defaults, if people do not update the klicky variables
    [klicky-macros.cfg]
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2022-05-21 updating STL's and CAD
    V1 was a wrong commig (was a carriage i was beta testing on a bed mounted dock, which needs to move up in Z to undock. the carriage was interfering with the gantry dock itself. fixed the CAD and STL's to work with the gantry mount.
    [Mantis_MGN12_KlickyNG_including_dock v4.step, carriage.stl]
2022-05-21 Update to support multiple probe types
    update to add KlickyNG in addition to Klicky
    [1mm_Spacer.stl, 2mm_NG_extender.stl, 2mm_extender.stl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]
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2022-05-23 added a homing override
    added a homing override to select what axis to home first
    [klicky-macros.cfg, klicky-variables.cfg]
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2022-05-26 Revert "Back away moves"
    [klicky-macros.cfg, klicky-variables.cfg]
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2022-05-27 enabled a very verbose debug output
    changed the default configuration to move away from the endstop by 10mm
    [klicky-macros.cfg, klicky-variables.cfg]
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2022-05-29 updated probe above the bed check
    corrects the error that does not allow to probe near the front of the bed
    [klicky-macros.cfg]
2022-05-29 update vcore3 readme
    Update klipper sections that were missing and causing klipper errors
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2022-06-02 corrected KlickyNG CAD
    [KlickyNGProbe v4.step, KlickyNGProbe_v4.step]
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2022-06-09 Revert "Merge branch 'main' into Switchwire-addon"
    This reverts commit d999c3ee2c7f2b7c69c02b6e1b1bad25ae44094e, reversing
    changes made to 38be544862f4f1c9437f29fa6b9744ec9e12c403.
    [2mm_extender.stl, Drive_arm_back.stl, Drive_arm_front.stl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]
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2022-06-10 commit problems correction
    [KlickyNG_UnklickyBFP_v1_Body.stl, KlickyNG_UnklickyBFP_v1_Body_3mm.stl, KlickyNG_UnklickyBFP_v1_Cap.stl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]
2022-06-12 X backoff behavior corrected on homing to X0
    [klicky-macros.cfg]
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2022-06-13 updated servo delay, helps solve timing issues
    [klicky-variables.cfg]
2022-06-15 resolved a bug an the servo test macro
2022-06-20 corrected safe_z behavior after a bed attached dock operation
    [klicky-macros.cfg]
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2022-06-24 Squashed commit of the following:
    commit e6da52b8c072c77afdc04c2d788829181107df4a
    Author: Jose Araujo <jlaraujo@mercs.homeip.net>
    Date: Fri Jun 24 21:38:55 2022 +0100
    default dock_on_zhome corrected, probe now docked at the end of homing
    commit b29aaa86ab1f27cd17a2ec30b5544cb7d58a85a0
    Author: Jose Araujo <jlaraujo@mercs.homeip.net>
    Date: Fri Jun 24 00:33:32 2022 +0100
    permits Z home with a probe attached
    commit 93b0b33bf0ba123a71b7288bdeeb3c682e1df242
    Author: Jose Araujo <jlaraujo@mercs.homeip.net>
    Date: Fri Jun 24 00:03:15 2022 +0100
    Update Klipper_macros.zip
    commit 77524e93d48b6409a5ca01a8b394298d56fe18cf
    Merge: f550ef6 f7fdd4e
    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
    [klicky-macros.cfg, klicky-variables.cfg]
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2022-06-26 directory changes and Read updates
    The CAD is also integrated on the main CAD, but as it's a binary file, i will update after merging.
    [EVA2_Klicky_mount.stl, EVA3_Klicky_mount.stl, Probe Dock v2.1.step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]
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2022-06-27 Z homing without z_hop bug correction
    [klicky-macros.cfg]
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2022-07-03 Fix broken Unklicky probe link
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2022-07-04 corrected _homing_x and y debug function
    [klicky-macros.cfg]
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2022-07-28 probe updates
    Klicky/Unklicky NG probes now have a reduced tilt, to improve accuracy
    NG dock is now shorter and lower, to help with docking issues
    [2mm_extender.stl, BFP Unklicky pin.stl, Drive_arm_back.stl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]
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2022-08-12 move Switchwire KlickyNG integrated carriage to the correct place
    [SW_X_Carriage_CW2_KlickyNG v1.step, SW_X_Carriage_CW2_KlickyNG.stl]
2022-08-14 corrected a too thin wall on the 3rd magnet
    [MGN12_X_Carriage_CW2_klickyNG v1.step, MGN12_X_Carriage_CW2_klickyNG v2.step, MGN12_X_Carriage_CW2_klickyNG.stl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]
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2022-09-30 Small non critical fixes in cad
    [KlickyNG_BFP_Unklicky_Pin.stl, KlickyNG_BFP_Unklicky_WhistlinRic_Back.stl, KlickyNG_BFP_Unklicky_WhistlinRic_Front_2p6mm.stl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]
2022-09-30 A few more refinements and a pin experiment
    M3 doesn't hold well enough - abandoned
    [KlickyNG_BFP_Unklicky_WhistlinRic_Back.stl, KlickyNG_BFP_Unklicky_WhistlinRic_Back2.stl, KlickyNG_BFP_Unklicky_WhistlinRic_Front2.stl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]
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2022-10-01 m3 cracked front - hole too tight with wire.
    [KlickyNG_BFP_Unklicky_WhistlinRic_Back.stl, KlickyNG_BFP_Unklicky_WhistlinRic_Front_2p6mm.stl, KlickyNG_BFP_Unklicky_WhistlinRic_Front_3mm.stl]
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2022-10-06 Clearance for probe wire, tighter m3 with wire clearance
    [KlickyNG_BFP_Unklicky_WhistlinRic_Back.stl, KlickyNG_BFP_Unklicky_WhistlinRic_Front_2p6mm.stl, KlickyNG_BFP_Unklicky_WhistlinRic_Front_3mm.stl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]
2022-10-07 Fix up stl - step files are not as good as I thought.
    [KlickyNG_BFP_Unklicky_Pin.stl, KlickyNG_BFP_Unklicky_Pin_3mm.stl]
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2022-11-21 solved added g28 bug added recently
    [klicky-macros.cfg]
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2022-11-24 corrected some parts orientation, grouped probes with zip
    [KlickyNG_Probe_insert.stl, V0_KlickyNG_probe_mount_insert_double.stl, V0_KlickyNG_probe_mount_insert_single.stl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]
2022-11-29 solved bug with Z virtual endstop
    [klicky-macros.cfg]
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2023-02-02 Fixed small typo in _Park_Toolhead macro
    [klicky-macros.cfg]
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2023-06-06 solved klicky-macros.cfg merge bug
    [klicky-macros.cfg]
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2023-07-09 Remove integer truncation from various positions
    This replaces the `|int` truncation of position and motion handling with
    `|float` so that fractional positions work.
    It also simplifies the code to do the conversion-to-float just once for
    each variable, rather than having many `|int`s scattered everywhere the
    variables are used.
    Fixes #159.
    [klicky-macros.cfg]
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2024-03-15 Adding missing [% %} to line 655
    [klicky-macros.cfg]
2024-03-15 corrected last chagne
    [klicky-macros.cfg]
2024-03-28 Fix goint typo (replace with going)
    [klicky-macros.cfg]
2024-06-15 Update klicky-macros.cfg
    Address an issue with blindly assuming that if Z is already homed then it is above safe_z which was overwriting the value of safe_z to the current Z position when re-homing if Z was already homed regardless of whether the current position was actually above the safe_z. Additionally included small typo fixes for logs.
    [klicky-macros.cfg]
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
